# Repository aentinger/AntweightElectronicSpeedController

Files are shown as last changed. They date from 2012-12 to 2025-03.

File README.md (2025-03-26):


💾 Antweight Electronic Speed Controller (ESC)
==============================================



Firmware of antweight electronic speed controller plus configuration software.

# 📸 Image

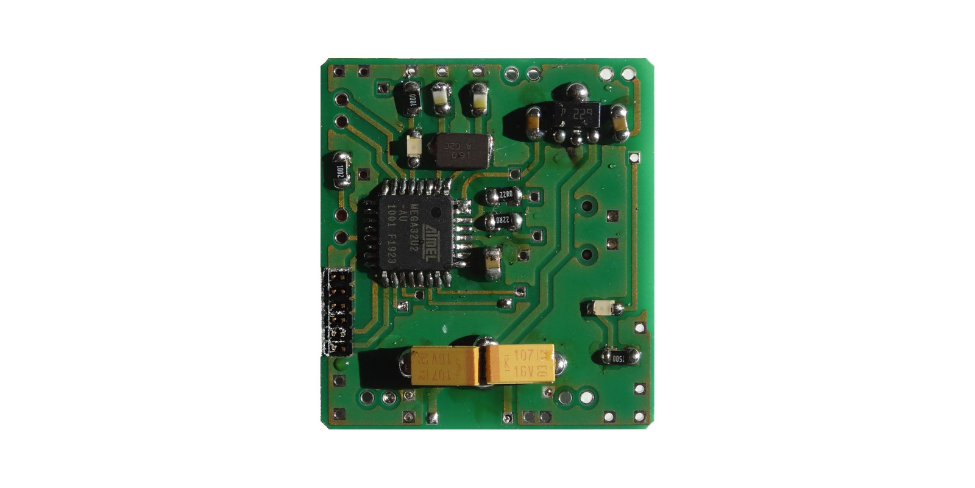
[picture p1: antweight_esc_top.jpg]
LXRobotics Antweight ESC


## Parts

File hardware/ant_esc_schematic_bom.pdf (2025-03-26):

Menge | Schaltplan | Bezeichnung | Farnell Bestell Nummer | Preis (1 Stück) * | Gesamtpreis
1 | ATMega8U2 | 1748535 | € | 3,42 | € | 3,42
1 | U$12 | Spannungsregler 5V, SOT89, L7805 | 1366573 | € | 0,37 | € | 0,37
2 | U$2, U$3 | SI9986CY-T1-E3 - IC, BUFFERED H-BRIDGE, 1A, 13.2V | 1612431 | € | 4,10 | € | 8,20
1 | D1 | Diode, ES2D, 2A, 200 V | 1625037 | € | 0,78 | € | 0,78
2 | U$8, U$9 | Tantal Kondensator, Bauform C, 100 uF, 16 V | 1793885 | € | 1,18 | € | 2,36
2 | C3, C4 | Keramik Kondensator, 0805, 18 pF, 100 V | 1740651 | € | 0,35 | € | 0,70
1 | C1 | Keramik Kondensator, 0805, 1 uF, 25 V | 1833845 | € | 0,60 | € | 0,60
3 | C2, C7 | Keramik Kondensator, 0805, 100 nF, 100 V | 1856515 | € | 0,07 | € | 0,21
1 | C6 | Keramik Kondensator, 0805, 330 nF, 100 V | 1833878 | € | 0,39 | € | 0,39
2 | R3, R6 | Widerstand, 10 kOhm, 125 mW, 0805 | 1469856 | € | 0,03 | € | 0,06
2 | R1, R2 | Widerstand, 22 Ohm, 100 mW, 0805 | 1652962 | € | 0,01 | € | 0,02
1 | R5 | Widerstand, 100 Ohm, 100 mW, 0805 | 1469862 | € | 0,03 | € | 0,03
1 | R4 | Widerstand, 150 Ohm, 100 mW, 0805 | 1469877 | € | 0,03 | € | 0,03
1 | Quarz, 16 MHz, SMD | 1611806 | € | 1,36 | € | 1,36
1 | USB SMD Verbinder, REICHELT | USB BWM SMD | € | 0,32 | € | 0,32 | REICHELT | FARNELL | 1125348
1 | U$13 | ISP Buchse, 1.27 mm, 6 Kontakte, 1 Reihe | 1803573 | € | 1,70 | € | 1,70
6 | U$4, U$11, U$5, U$6, U$10 | 2-Pin, 2,54 mm, Steckverbinder | 9731075 | € | 0,18 | € | 1,08
1 | LED2 | OSRAM, CHIPLED, 0805, Gelb, 2V, 20 mA, LY R976 | 153392 - 62 | € | 0,15 | € | 0,15 | CONRAD
1 | LED1 | OSRAM, CHIPLED, 0805, Rot, 2V, 20 mA, LS R976 | 153391 - 62 | € | 0,15 | € | 0,15 | CONRAD
1 | Leiterplatte, Beidseitig, 31 x 34 mm, LeitOn | | € | 7,08 | € | 7,08
| | | Summe | | € | 29,01

* Anteilige Versandkosten und Mengenrabatte für Preis von einem Stück bereits einberechnet

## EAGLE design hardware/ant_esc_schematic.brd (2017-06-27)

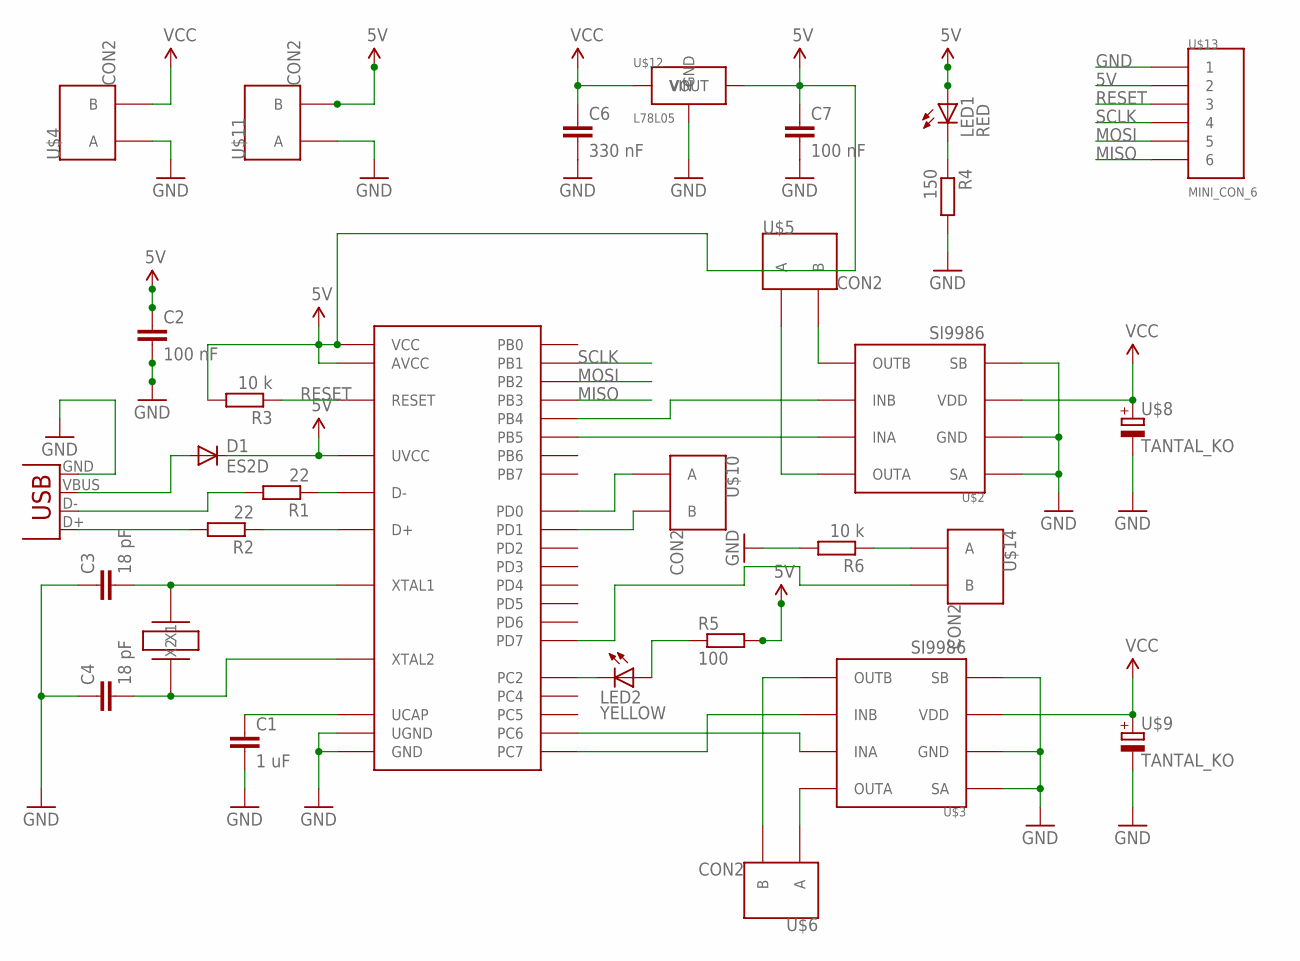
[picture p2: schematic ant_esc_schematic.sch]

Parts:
C1: 1 uF; C0805
C2, C7: 100 nF; C0805
C3, C4: 18 pF; C0805
C6: 330 nF; C0805
D1: ES2D; SMB
JP1: USBSMD; USB-MINIB
LED1: RED; CHIPLED_0805
LED2: YELLOW; CHIPLED_0805
R1, R2: 22; M0805
R3, R6: 10 k; M0805
R4: 150; M0805
R5: 100; M0805
U$1: ATMEGA8U2; TQFP32-08
U$2, U$3: SI9986; SOIC8
U$4, U$5, U$6, U$10, U$11, U$14: CON2; 332-02
U$7: 16 MHz; ABM3
U$8, U$9: TANTAL_KO; KEMET_C
U$12: L78L05; SOT89
U$13: MINI_CON_6; MIN_CON_6

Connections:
5V: C2.1, C7.1, D1.C, LED1.A, R3.2, R5.2, U$1.AVCC, U$1.UVCC, U$1.VCC, U$11.2 (B), U$12.VOUT, U$13.2
GND: C1.2, C2.2, C3.1, C4.1, C6.2, C7.2, JP1.GND, R4.2, R6.2, U$1.GND, U$1.UGND, U$2.GND, U$2.SA, U$2.SB, U$3.GND, U$3.SA, U$3.SB, U$4.1 (A), U$8.CATHODE- (-), U$9.CATHODE- (-), U$11.1 (A), U$12.2@1 (GND), U$12.GND, U$13.1
MISO: U$1.PB3, U$13.6
MOSI: U$1.PB2, U$13.5
unnamed: R1.1, U$1.D-
unnamed: R2.1, U$1.D+
unnamed: JP1.D+, R2.2
unnamed: D1.A, JP1.VBUS
unnamed: JP1.D-, R1.2
unnamed: C1.1, U$1.UCAP
unnamed: U$1.PD0, U$10.1 (A)
unnamed: U$1.PB5, U$2.INA
unnamed: U$1.PB4, U$2.INB
unnamed: U$1.PC6, U$3.INA
unnamed: U$1.PC7, U$3.INB
unnamed: U$3.OUTA, U$6.1 (A)
unnamed: U$3.OUTB, U$6.2 (B)
unnamed: U$2.OUTB, U$5.2 (B)
unnamed: U$2.OUTA, U$5.1 (A)
unnamed: LED1.C, R4.1
unnamed: LED2.C, U$1.PC2
unnamed: C4.2, U$1.XTAL2, U$7.X1
unnamed: C3.2, U$1.XTAL1, U$7.X2
unnamed: U$1.PD1, U$10.2 (B)
unnamed: U$1.PD7, U$14.2 (B)
unnamed: LED2.A, R5.1
unnamed: R6.1, U$14.1 (A)
RESET: R3.1, U$1.RESET, U$13.3
SCLK: U$1.PB1, U$13.4
VCC: C6.1, U$2.VDD, U$3.VDD, U$4.2 (B), U$8.ANODE+ (+), U$9.ANODE+ (+), U$12.VIN

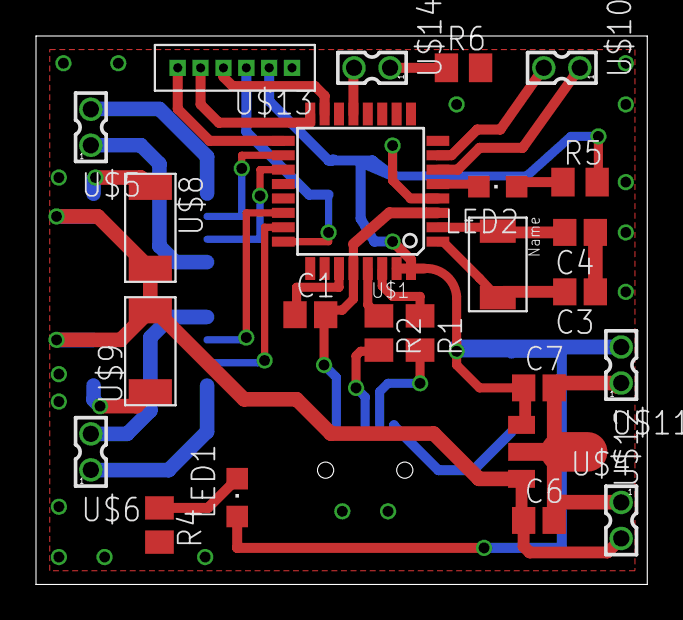
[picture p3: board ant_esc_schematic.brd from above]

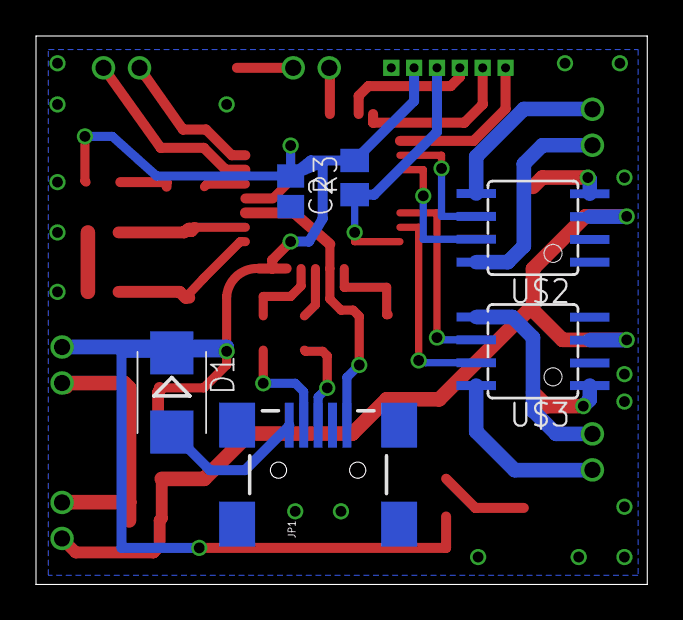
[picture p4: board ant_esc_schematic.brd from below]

Board: 2 copper layers, 34.0 x 30.5 mm, 30 parts (6 on the bottom side), 30 nets.

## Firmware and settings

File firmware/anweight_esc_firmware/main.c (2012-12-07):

/*
	Copyright 2013 by Alexander Entinger, BSc

    This file is part of antweight_esc_firmware.

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
    You should have received a copy of the GNU General Public License
    along with antweight_esc_firmware.  If not, see <http://www.gnu.org/licenses/>.
*/

/**
* @author Alexander Entinger, BSc
* @brief main file for antweight electronic speed control firmware
* @file main.cpp
*/

#include <avr/interrupt.h>
#include <stdint.h>
#include <stdbool.h>
#include "motor_control.h"
#include "input.h"
#include "control.h"
#include "config.h"
#include "status_led.h"
#include "VirtualSerial/VirtualSerial.h"

// configuration structure
volatile s_config_data configuration;
// flag to tell control module to perform calibration of neutral position
volatile bool do_calibration_of_neutral_position = false;

/**
* @brief initializes the whole application
*/
void init_application();

typedef enum {INIT = 0, ACTIVE = 1, CALIBRATION = 2, FAILSAFE = 3, CONFIG = 4, ERROR = 5} E_FIRMWARE_STATE;

int main(void) {
	
	init_application();

	uint8_t firmware_state = INIT;
	
	for(;;) {
	
		switch(firmware_state) {
			case INIT: {
				while(!input_good()) {
					// wait until we have a good signal
					// do the usb task necessary for working the usb
					virtual_serial_task();
					// if we have data available, switch the firmware state to go to config mode
					if(virtual_serial_bytes_available()) {
						firmware_state = CONFIG;
						break;
					}
				}				 
				if(firmware_state == INIT) {
					firmware_state = CALIBRATION;
				}
			}	break;
			case CALIBRATION: {
				// now do the calibration, set the config flag
				do_calibration_of_neutral_position = true;
				while(do_calibration_of_neutral_position) {
					// wait for calibration to be done
				}
				// and switch over to avtive state
				firmware_state = ACTIVE;
			} break;
			case ACTIVE: {
				// the input signals are switch to the output signals depending on the driving mode (tank or v mixer)
				// monitor the signals, if there are no pulses on both channels for 5 periods switch to failsafe mode
				enable_motors();
				// turn on status led to signalize operation
				status_led_turn_on();
				while(input_good()) {
					// do the control stuff here, since its interrupt controlled nothing to do here anymore
				}
				firmware_state = FAILSAFE; // input channels are bad, switch to failsafe
			} break;
			case FAILSAFE: {
				// we are in failsafe, so switch of the output channels
				disable_motors();
				// also turn off status led to signal that we are not in active state anylonger
				status_led_turn_off();
				while(!input_good()) {
					// wait until the signals are back up, if thats the case switch back to active
				}
				firmware_state = ACTIVE;
			} break;
			case CONFIG: {
				// do the config, no disabling of the motors needed, since they are not yet enabled
				bool config_done = false;
				do {
					// do the usb task necessary for working the usb
					virtual_serial_task();
					// read from usb, change the settings according to that and send the requests answers
					if(virtual_serial_bytes_available()) {
						uint8_t data_byte = 0;
						if(virtual_serial_receive_byte(&data_byte)) {
							config_parse_data(data_byte, &config_done);
						}
					}
				} while(!config_done);				
				// then go back to init
				firmware_state = INIT; 
			} break;
			case ERROR: {
				// if we should land hear, whatever the reason, switch all output off
				disable_motors();
				// turn status led off, no valid operation mode
				status_led_turn_off();
				// no way leads out of here
				for(;;) { asm("NOP"); }
			} break;
			default: {
				firmware_state = ERROR;
			} break;
		}
	}
}

/**
* @brief initializes the whole application
*/
void init_application() {

	// load parameters from EEPROM
	init_config();
	
	// initialize motor control
	init_motor_control();
	
	// init the contro module
	init_control();
	
	// initialize the input module and register the callbacks
	init_input(control_ch1_data_callback, control_ch2_data_callback);
	
	// initialize the virtual serial
	init_virtual_serial();
	
	// initialize the status led
	init_status_led();
	
	// enable globally interrupts
	sei();
}

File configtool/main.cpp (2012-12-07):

/*
	Copyright 2013 by Alexander Entinger, BSc

    This file is part of escconfig.

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
    You should have received a copy of the GNU General Public License
    along with escconfig.  If not, see <http://www.gnu.org/licenses/>.
*/

/**
 * @author Alexander Entinger, BSc
 * @brief main file for antweight esc configuration tool
 * @file main.cpp
 */

#include <iostream>
#include <stdlib.h>
#include <string>
#include <stdexcept>
#include "serial.h"
#include "args.h"
#include "configuration.h"

void print_help() {
	std::cout << "Usage: escconfig DEVICE_NODE [ARGS]" << std::endl;
	std::cout << "\tDEVICE_NODE\tname of the serial port occupied by the device,\n\t\t\te.g. COM3 in Windows or /dev/ttyACM0 in Linux" << std::endl;
	std::cout << "\t-help\t\tget this help file" << std::endl;
	std::cout << "\t-display\tshows the current configuration of the speed controller" << std::endl;
	std::cout << "\t-control-tank\tset control method to tank steering" << std::endl;
	std::cout << "\t-control-delta\tset control method to delta steering" << std::endl;
	std::cout << "\t-deadzone-VALUE\tset the deadzone value to the value VALUE (around 0.1 ms)" << std::endl;
	std::cout << "\t-ch1-min-value-VALUE\tset the minimum value of the remote control of ch 1 (around 1.0 ms)" << std::endl;
	std::cout << "\t-ch1-max-value-VALUE\tset the maximum value of the remote control of ch 1 (around 2.0 ms)" << std::endl;
	std::cout << "\t-ch2-min-value-VALUE\tset the minimum value of the remote control of ch 2 (around 1.0 ms)" << std::endl;
	std::cout << "\t-ch2-max-value-VALUE\tset the maximum value of the remote control of ch 2 (around 2.0 ms)" << std::endl;
}


void checked_main(int const argc, char **argv) {

	bool display_configuration = false;

	args arg_cont(argc, argv);

	serial::get_instance().init(arg_cont.get_dev_node(), 115200);

	configuration conf;

	while(!arg_cont.empty()) {
		std::string const arg = arg_cont.get_next_argument();

		size_t deadzone = 0;
		size_t rc_val = 0;
		if(args::is_help(arg)) {
			print_help();
			throw std::runtime_error("Hopefully the help helped you. Exiting program.");
		}
		else if(args::is_control_tank(arg)) conf.get()->control = TANK;
		else if(args::is_control_delta(arg)) conf.get()->control = DELTA;
		else if(args::is_deadzone(arg, &deadzone)) conf.get()->deadzone = deadzone;
		else if(args::is_rc_ch1_min(arg, &rc_val)) {
			conf.get()->remote_control_min_value_ch1 = rc_val;
			conf.update();
		}
		else if(args::is_rc_ch1_max(arg, &rc_val)) {
			conf.get()->remote_control_max_value_ch1 = rc_val;
			conf.update();
		}
		else if(args::is_rc_ch2_min(arg, &rc_val)) {
			conf.get()->remote_control_min_value_ch2 = rc_val;
			conf.update();
		}
		else if(args::is_rc_ch2_max(arg, &rc_val)) {
			conf.get()->remote_control_max_value_ch2 = rc_val;
			conf.update();
		}
		else if(args::is_display_configuration(arg)) display_configuration = true;
		else throw std::runtime_error("Argument not valid. Exiting program.");
	}

	if(display_configuration) { // no writing when we read, otherwise the interface gets to confusing
		std::cout << conf;
	} else {
		conf.write();
	}

	// cleanup
	serial::destroy();
}

int main(int argc, char **argv) {

	try {
		checked_main(argc, argv);
	} catch(std::exception &e) {
		std::cerr << e.what() << std::endl;
		return EXIT_FAILURE;
	} catch(...) {
		std::cerr << "Unhandled exception caught, exiting programm." << std::endl;
		return EXIT_FAILURE;
	}

	return EXIT_SUCCESS;
}

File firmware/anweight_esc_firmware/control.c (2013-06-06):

/*
Copyright 2013 by Alexander Entinger, BSc

This file is part of antweight_esc_firmware.

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
You should have received a copy of the GNU General Public License
along with antweight_esc_firmware.  If not, see <http://www.gnu.org/licenses/>.
*/

/**
* @author Alexander Entinger, BSc
* @brief this file implements the control unit of the firmware, doing the appopriate signal conditioning from the input signals for the motor control
* @file control.cpp
*/

#include "control.h"
#include "motor_control.h"
#include "config.h"
#include "linear_mapper.h"
#include "linear_mapper_2d.h"
#include "filter.h"

// calibration flag for defining when calibration of neutral position is done
extern bool do_calibration_of_neutral_position;
// channel selection
typedef enum {CH1 = 0, CH2 = 1} E_CHANNEL_SELECT;
// maximum channel value
static uint16_t const MAX_CHANNEL_VALUE = 500; // max 2 ms pulsewidth
// adt data for the linear mapper
static linear_mapper map_ch1_fwd, map_ch1_bwd, map_ch2_fwd, map_ch2_bwd;
// adt date for the linear mapper in 2 dimensions
static linear_mapper_2d map_motor_left_2d, map_motor_right_2d;
// adt data for the filter
static filter filt[2];
	
/**
 * @brief this class is called when new data has arrived - its job is to calculate new data and transmit it to the motor drivers
 */
void control_update();
/** 
 * @brief provides a conditioning of the signal from the linear mapper to the motor control
 */
uint8_t speed_conditioning(int16_t const s);

/** 
 * @brief initializes the control module
 */
void init_control() {
	init_filter(&filt[CH1], 4, 125);
	init_filter(&filt[CH2], 4, 125);
	
	init_linear_mapper_2d(&map_motor_left_2d, -16320, -65, -65);
	init_linear_mapper_2d(&map_motor_right_2d, 0, -65, 65);
}

/**
 * @brief updates the linear mapper 2 functions after a configuration via the pc
 */ 
void update_linear_mapper_2d() {
	init_linear_mapper_2d(&map_motor_left_2d, configuration.r1, configuration.s1, configuration.t1);
	init_linear_mapper_2d(&map_motor_right_2d, configuration.r2, configuration.s2, configuration.t2);
}

/**
 * @brief callback function called when new data on channel 1 arrived
 */
void control_ch1_data_callback(uint16_t const pulse_duration) {
	if(pulse_duration <= MAX_CHANNEL_VALUE) {
		// subtract the 1 ms minimum pulsewidth which we always have, equals pulse_duration - 250, the max value of pulse_duration is thereby 250
		filter_add_value(&filt[CH1], pulse_duration - (MAX_CHANNEL_VALUE >> 1));
		// call the update function
		control_update();
	}		
}	
	
/**
 * @brief callback function called when new data on channel 2 arrived
 */
void control_ch2_data_callback(uint16_t const pulse_duration) {
	if(pulse_duration <= MAX_CHANNEL_VALUE) {
		// subtract the 1 ms minimum pulsewidth which we always have, equals pulse_duration - 250, the max value of pulse_duration is thereby 250
		filter_add_value(&filt[CH2], pulse_duration - (MAX_CHANNEL_VALUE >> 1));
		// call the update function
		control_update();
	}
}

/** 
 * @brief provides a conditioning of the signal from the linear mapper to the motor control
 */
uint8_t speed_conditioning(int16_t const s) {
	int16_t speed = s;
	speed >>= 5;
	if(speed < 0) speed = 0;
	else if(speed > 255) speed = 255;
	return (uint8_t)(speed);
}

/**
 * @brief this class is called when new data has arrived - its job is to calculate new data and transmit it to the motor drivers
 */
void control_update() {
	// initial middle value of the channels
	static int16_t MIDDLE_VALUE_CH[2] = {125, 125};
	// values for calibrating offsets from the middle value in delta mode
	static int16_t OFFSET_CH[2] = {0,0};
	
	// do the calibration of the neutral position
	if(do_calibration_of_neutral_position) {
		MIDDLE_VALUE_CH[CH1] = filter_get_value(&filt[CH1]);
		MIDDLE_VALUE_CH[CH2] = filter_get_value(&filt[CH2]);
		// configuration done
		do_calibration_of_neutral_position = false;	
		// adjust the linear mapping modules
		init_linear_mapper(&map_ch1_bwd, configuration.remote_control_min_value_ch_1, MIDDLE_VALUE_CH[CH1], MAX_MOTOR_VALUE, 0);
		init_linear_mapper(&map_ch1_fwd, MIDDLE_VALUE_CH[CH1], configuration.remote_control_max_value_ch_1, 0, MAX_MOTOR_VALUE);
		init_linear_mapper(&map_ch2_bwd, configuration.remote_control_min_value_ch_2, MIDDLE_VALUE_CH[CH2], MAX_MOTOR_VALUE, 0);
		init_linear_mapper(&map_ch2_fwd, MIDDLE_VALUE_CH[CH2], configuration.remote_control_max_value_ch_2, 0, MAX_MOTOR_VALUE);
		// calculate offset values for correcting offsets in delta mode
		OFFSET_CH[CH1] = (int16_t)(125) - MIDDLE_VALUE_CH[CH1];
		OFFSET_CH[CH2] = (int16_t)(125) - MIDDLE_VALUE_CH[CH2];
		// exit function here
		return;
	}
	
	uint16_t const m_ch_value[2] = {filter_get_value(&filt[CH1]), filter_get_value(&filt[CH2])};
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

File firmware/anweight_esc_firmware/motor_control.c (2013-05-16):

/*
	Copyright 2013 by Alexander Entinger, BSc

    This file is part of antweight_esc_firmware.

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
    You should have received a copy of the GNU General Public License
    along with antweight_esc_firmware.  If not, see <http://www.gnu.org/licenses/>.
*/

/**
* @author Alexander Entinger, BSc
* @brief this file represents a motor control for the two channels of the esc
* @file motor_control.cpp
*/

#include "motor_control.h"

#include <avr/io.h>
#include <avr/interrupt.h>

static volatile E_MOTOR_STATE m_motor_state = DISABLED;
static volatile E_MOTOR_DIRECTION m_motor_left_dir = FWD;
static volatile E_MOTOR_DIRECTION m_motor_right_dir = FWD;

#define MOTOR_LEFT_A_PIN	(6)
#define MOTOR_LEFT_A_DDR	(DDRC)
#define MOTOR_LEFT_A_PORT	(PORTC)
#define MOTOR_LEFT_B_PIN	(7)
#define MOTOR_LEFT_B_DDR	(DDRC)
#define MOTOR_LEFT_B_PORT	(PORTC)

#define MOTOR_RIGHT_A_PIN	(5)
#define MOTOR_RIGHT_A_DDR	(DDRB)
#define MOTOR_RIGHT_A_PORT	(PORTB)
#define MOTOR_RIGHT_B_PIN	(4)
#define MOTOR_RIGHT_B_DDR	(DDRB)
#define MOTOR_RIGHT_B_PORT	(PORTB)

/**
* @brief initializes the motor control object
*/
void init_motor_control() {
	// set value of als Pins to '0'
	MOTOR_LEFT_A_PORT  &= ~(1<<MOTOR_LEFT_A_PIN);
	MOTOR_LEFT_B_PORT  &= ~(1<<MOTOR_LEFT_B_PIN);
	MOTOR_RIGHT_A_PORT &= ~(1<<MOTOR_RIGHT_A_PIN);
	MOTOR_RIGHT_B_PORT &= ~(1<<MOTOR_RIGHT_B_PIN);
	
	// set all pins to output
	MOTOR_LEFT_A_DDR  |= (1<<MOTOR_LEFT_A_PIN);
	MOTOR_LEFT_B_DDR  |= (1<<MOTOR_LEFT_B_PIN);
	MOTOR_RIGHT_A_DDR |= (1<<MOTOR_RIGHT_A_PIN);
	MOTOR_RIGHT_B_DDR |= (1<<MOTOR_RIGHT_B_PIN);
	
	// enable output compare interrupt a and b and timer 1 overflow interrupt
	TIMSK0 = (1<<OCIE0A) | (1<<OCIE0B) | (1<<TOIE0);
	
	// Timer 0: f = 16 MHz
	// Prescaler = 64 => tTimerStep = 4 us
	// fPWM = 1 kHz, Reload Value = 250
	TCCR0B = (1<<CS01) | (1<<CS00);
}

/**
* @brief enables the motor outputs
*/
void enable_motors() {
	m_motor_state = ENABLED;
}

/**
* @brief disables the motor outputs (both Motor + and - are at zero)
*/
void disable_motors() {
	m_motor_state = DISABLED;
	// disable the motors
	MOTOR_LEFT_A_PORT  &= ~(1<<MOTOR_LEFT_A_PIN);
	MOTOR_LEFT_B_PORT  &= ~(1<<MOTOR_LEFT_B_PIN);
	MOTOR_RIGHT_A_PORT &= ~(1<<MOTOR_RIGHT_A_PIN);
	MOTOR_RIGHT_B_PORT &= ~(1<<MOTOR_RIGHT_B_PIN);
}

/**
* @brief sets the pwm value of the left motor
* @param dir movement direction of the motor: either forward of backward
* @param s speed value between 0 and 255 (0 % to 100 %), speed of 0 = BRAKE
*/
void set_pwm_motor_left(E_MOTOR_DIRECTION const dir, uint8_t const s) {
	uint16_t speed = s;
	if(s == 0) {
		TIMSK0 &= ~(1<<OCIE0A);
	}
	else {
		OCR0A = 255 - speed;
		TIMSK0 |= (1<<OCIE0A);
	}
	m_motor_left_dir = dir;
}

/**
* @brief sets the pwm value of the right motor
* @param dir movement direction of the motor: either forward of backward
* @param s speed value between 0 and 255 (0 % to 100 %), speed of 0 = BRAKE
*/
void set_pwm_motor_right(E_MOTOR_DIRECTION const dir, uint8_t const s) {
	uint16_t speed = s;
	if(s == 0) {
		TIMSK0 &= ~(1<<OCIE0B);
	}
	else {
		OCR0B = 255 - speed;
		TIMSK0 |= (1<<OCIE0B);
	}
	m_motor_right_dir = dir;
}

/**
* @brief ISR for Timer 0 overflow vector
*/
ISR(TIMER0_OVF_vect) {
	// switch the motors off
	MOTOR_LEFT_A_PORT  &= ~(1<<MOTOR_LEFT_A_PIN);
	MOTOR_LEFT_B_PORT  &= ~(1<<MOTOR_LEFT_B_PIN);
	MOTOR_RIGHT_A_PORT &= ~(1<<MOTOR_RIGHT_A_PIN);
	MOTOR_RIGHT_B_PORT &= ~(1<<MOTOR_RIGHT_B_PIN);
}

/**
* @brief ISR for output compare channel A (left motor)
*/
ISR(TIMER0_COMPA_vect) {
	if(m_motor_state == ENABLED) {
		if(m_motor_left_dir == FWD) {
			MOTOR_LEFT_A_PORT  |= (1<<MOTOR_LEFT_A_PIN);
		} else if(m_motor_left_dir == BWD) {
			MOTOR_LEFT_B_PORT  |= (1<<MOTOR_LEFT_B_PIN);
		}
	}
}

/**
* @brief ISR for output compare channel B (right motor)
*/
ISR(TIMER0_COMPB_vect) {
	if(m_motor_state == ENABLED) {
		if(m_motor_right_dir == FWD) {
			MOTOR_RIGHT_A_PORT  |= (1<<MOTOR_RIGHT_A_PIN);
		} else if(m_motor_right_dir == BWD) {
			MOTOR_RIGHT_B_PORT  |= (1<<MOTOR_RIGHT_B_PIN);
		}
	}
}

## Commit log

2012-12-07 adding sourcoce for config tool
    [configuration.h]
2012-12-07 adding configuration functionality for delta mixer code
    [configuration.h]
2013-05-17 introducing a calibration state for simplicity of understanding the fsm
2013-05-20 added filtering functionality for antweight firmware
2013-05-21 added status led for signalising active and nonactive states
2013-05-21 corrected typo in configuration.cpp
    [configuration.cpp]
2013-05-29 adding calibration of neutral position for delta mode
2017-06-27 Adding hardware + images
    [ant_esc_schematic.brd, ant_esc_schematic.sch]
2025-03-26 Add BOM.
2025-03-26 Adding picture of prototype.

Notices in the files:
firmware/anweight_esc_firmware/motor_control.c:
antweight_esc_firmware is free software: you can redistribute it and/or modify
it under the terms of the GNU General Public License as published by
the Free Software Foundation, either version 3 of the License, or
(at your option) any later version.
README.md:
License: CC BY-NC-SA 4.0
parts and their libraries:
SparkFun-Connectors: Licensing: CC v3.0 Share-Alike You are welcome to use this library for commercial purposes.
